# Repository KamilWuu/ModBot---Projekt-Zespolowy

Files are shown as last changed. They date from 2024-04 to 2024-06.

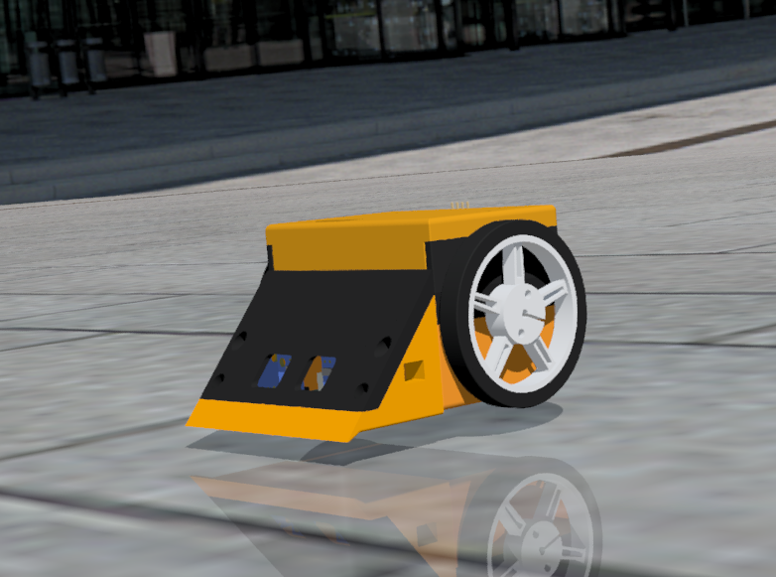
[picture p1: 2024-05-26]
images/render_!.png

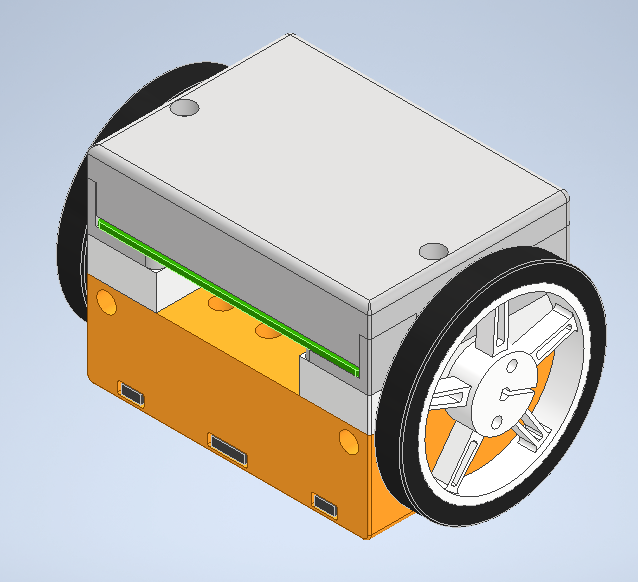
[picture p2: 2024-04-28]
images/main_module.png

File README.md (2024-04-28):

# ModBot---Projekt-Zespolowy


1 - Założenia projektowe
Robot modułowy ModBot będzie złożony z jednostki głównej – Platformy Mobilnej wraz z pilotem zdalnego sterowania za pomocą technologii Bluetooth. Platforma ta będzie miała możliwość
doczepienia modułów określających przeznaczenie robota:

• moduł MiniSumo,

• moduł LineFollower,

• Chwytak

2 - Cel i zakres projektu
Celem projektu jest stworzenie uniwersalnej platformy robotycznej pozwalającej na edukację
w zakresie elektroniki i programowania. Osobie uczącej się przy pomocy robota będzie da-
na możliwość samodzielnego złożenia oraz zamontowania wcześniej przygotowanych modułów,
dzięki którym robot będzie mógł wykonywać określone zadanie. Planowane są trzy domyślne
konfiguracje, za pomocą których robot będzie mógł wykonać następujące zadania:

• LineFollower – podążanie wzdłuż czarnej linii kontrastowej na białym tle, która nie posiada
zakrętów ostrzejszych niż 90◦.

• RoboSumo – przesunięcie kostki o masie zbliżonej do masy robota z standardowego ringu
Minisumo i pozostanie na ringu. Ma to na celu symulacje walki z zawodów robotycznych
z kategorii MiniSumo.

• Chwytak – utrzymanie obiektu o znacznie mniejszej masie niż jego własne poprzez moduł
zdalnego sterowania.

3 - Skład zespołu:
Kamil Winnicki - Mechanika i embedded,

Oliwier Woźniak -  Elektronika,

Patryk Peroński - Oprogramowanie i embeeded,

Rafał Koziołek - Mechanika i elektronika,

Jakub Frąckowiak - Kierownik zespołu, organizacja pracy,

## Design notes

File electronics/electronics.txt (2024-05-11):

Zanim zaczniecie cokolwiek robić, prosiłbym o posprzątanie warsztatu mechanicznego. Nawet jeśli NIE BĘDZIE "wielkiego sprzątania piwnicy". Przy czym nie mówie tu odrazu że macie zrobić wszystko na błysk.  Obecnie narzędzia rozwalone są po całej piwnicy i randomowych case'ach a piwnica jest cała w wiórach. 
PS. Gajowy nie jest od tego żeby po wszystkich sprzątać, a smieci można wyrzucić bez jego ingerencji.

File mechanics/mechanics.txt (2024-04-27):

backend i frontend - java script

Framework - react mui

czysty mysql

HOTEL:
- piętra, numer pokoju - numer pokoju zaczyna się od piętra

Pokoj
- numer pokoju
- pietro
- liczba lozek
- liczba miejsca
- standard pokoju
- cena za osobe
- cena za pokoj
- kuchnia czy jest

Rezerwacja:
mozna wyszukac po wlasnosciach pokoju, po liczbie miejsc
wpisywac ludzi co drugi pokoj
- data

aplikacja webowa

sortowanie
filtr
cena itp

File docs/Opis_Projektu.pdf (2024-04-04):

## Politechnika Wrocławska

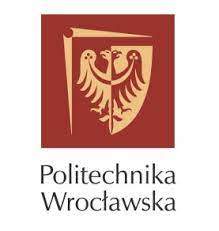
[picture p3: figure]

### Projekt Zespołowy Robot Modułowy ModBot

### Wydział: W12N Prowadzący: Dr inż. Robert Muszyński

Autorzy:

Kamil Winnicki
Oliwier Woźniak
Patryk Peroński
Rafał Koziołek
Jakub Frąckowiak
Wrocław, Polska | 4 kwietnia 2024

### Spis treści

1 Założenia projektowe | 1
2 Plan pracy i rozkład w czasie | 2
3 Doręczenie | 3
4 Budżet | 3
5 Zarządzanie projektem | 4
6 Skład zespołu | 4

### 1 Założenia projektowe

Robot modułowy ModBot będzie złożony z jednostki głównej – Platformy Mobilnej wraz z pilotem zdalnego sterowania za pomocą technologii Bluetooth. Platforma ta będzie miała możliwość doczepienia modułów określających przeznaczenie robota:
- moduł MiniSumo,
- moduł LineFollower,
- Chwytak.

### 1.1 Cel i zakres projektu

Celem projektu jest stworzenie uniwersalnej platformy robotycznej pozwalającej na edukację w zakresie elektroniki i programowania. Osobie uczącej się przy pomocy robota będzie dana możliwość samodzielnego złożenia oraz zamontowania wcześniej przygotowanych modułów, dzięki którym robot będzie mógł wykonywać określone zadanie. Planowane są trzy domyślne konfiguracje, za pomocą których robot będzie mógł wykonać następujące zadania:
- LineFollower – podążanie wzdłuż czarnej linii kontrastowej na białym tle, która nie posiada zakrętów ostrzejszych niż 90◦
- RoboSumo – przesunięcie kostki o masie zbliżonej do masy robota z standardowego ringu Minisumo i pozostanie na ringu. Ma to na celu symulacje walki z zawodów robotycznych z kategorii MiniSumo.
- Chwytak – utrzymanie obiektu o znacznie mniejszej masie niż jego własne poprzez moduł zdalnego sterowania.

### 1.2 Mechanika

W celu wzbudzenia większego zainteresowania wśród potencjalnych odbiorców, konstrukcja będzie składać się z wcześniej przygotowanych przez nas ”bloków”, w pewnym stopniu pozwalających na dostosowanie wyglądu takiego robota. Wykonane one bedą głównie z materiałów używanych powszechnie w druku 3D takich jak PLA lub PET-G.
W układzie napędowym robota zostaną zastosowane dwa silniki szczotkowe typu Pololu N20, które będą sterowane za pomocą układu różnicowego. W module chwytaka zostanie zastosowany serwomechanizm o wadze dziewięciu gramów.

### 1.3 Elektronika

Elektronika jako główną jednostkę obliczeniową będzie używać mikrokontrolera ESP32 - S3, ze względu na wbudowaną antenę WiFi/Bluetooth oraz prostotę implementacji.
Do sterowania silnikami zostanie zastosowany sterownik TB6612FNG, zawierający m.in podwójny mostek H.
W module MiniSumo użyte zostaną czujniki laserowe VL53L0X oraz dwa czujniki odbiciowe KTIR0711S. Zostaną one także użyte w module LineFollower w ilości 12 sztuk.

### 1.4 Oprogramowanie

Projekt zakłada programowanie Platformy Mobilnej za pomocą prostego środowiska graficznego korzystającego z bloków funkcyjnych. Program zostanie napisany w języku Scratch ze względu na popularność w sektorze edukacyjnym, prostotę obsługi oraz wsparcie dla dodatkowych rozszerzeń.
Program będzie kompatybilny ze środowiskiem Arduino, zapewniający podstawowe bloki funkcyjne m.in do odczytu czy ustawiania pinów, odczytów wejść analogowych, sterowaniu wyjściami PWM oraz obsłudze bibliotek pod popularne urządzenia peryferyjne takie jak: czujniki odległości TOF VL53L0X, serwomechanizmów i czujników laserowych.
Środowisko zapewni gotowe bloczki do obsługi modułów robota, dzięki którym nawet osoby bez doświadczenia w programowaniu powinny być w stanie zaprogramować swojego robota.

### 2 Plan pracy i rozkład w czasie

Ze względu na modułowość projektu, logicznym jest podział projektu na segmenty spełniających konkretne funkcje. W związku z tym nasz projekt podzieliliśmy na następujące zadania:
1. ustalenie interfejsów łączących poszczególne moduły,
2. zaprojektowanie i stworzenie głównego modułu sterującego,
3. napisanie i wdrożenie środowiska do programowania blokowego,
4. zaprojektowanie i stworzenie modułu napędowego,
5. zaprojektowanie i stworzenie modułu LineFollowera,
6. zaprojektowanie i stworzenie modułu MiniSumo,
7. zaprojektowanie i stworzenie modułu chwytaka oraz pilota służącego do zdalnego sterowania.

### 2.1 Kamienie milowe

Jak widać wszystkie te punkty (z wyjątkiem punktu pierwszego) podzielone są na dwa etapy, dzielące się na planowanie i realizację. Wszystkie te zadania, a w szczególności trzy ostatnie, mogą być wykonywane równolegle. Jednak preferowany jest tryb wykonywania zadań zgodny z powyższą numeracją. Zadania złożyliśmy na konkretne kamienie milowe.
Cechą tego rozwiązania jest złożoność zadań – składają się one z dwóch etapów: planowania i realizacji. Ponadto modułowość projektu sprawia, że punkty mogą być wykonywane równolegle i niezależnie od siebie. Jednak preferowany jest tryb wykonywania zadań zgodny z powyższą numeracją. Zadania zostały rozłożone na konkretne kamienie milowe.

### 2.1.1 Zakończenie fazy projektowej

Etap polega na stworzeniu schematów oraz przetestowaniu konkretnych elementów modułów. Po zakończeniu tego etapu będzie można zamówić wszystkie elementy elektroniczne oraz płytki PCB.

### 2.1.2 Synteza fizycznej części projektu

Po otrzymaniu płytek PCB oraz elementów elektronicznych zostaną rozpoczęte testy pojedynczych modułów. Działające płytki zostaną połączone i przetestowane za pomocą prostych programów. Kamień milowy zostanie osiągnięty, w momencie kiedy sygnały wysyłane z modułu głównego układu spotkają się z pożądaną reakcją modułu sterowanego (na przykład silniki będą się kręciły w odpowiednią stronę i zadaną prędkością).

### 2.1.3 Połączenie części fizycznej oraz programowej

Efektem tego etapu będzie gotowy produkt. Poprawne działanie robota po tym etapie oznaczać będzie osiągnięcie celu.

### 3 Doręczenie

Praca będzie jawna, dokumenty i efekty końcowe będą publikowane na platformie GitHub. Doręczenie projektu będzie odpowiadało etapom produkcji, zwieńczonymi realizacją kamieni milowych. Gdy kamień milowy zostanie osiągnięty, będzie wysłany dokument potwierdzający realizacje, zawierający następujące punkty:
- wskazanie co było kamieniem milowym,
- sposób realizacji,
- program oraz zdjęcia modułu robota,
- problemy oraz sposoby ich rozwiązania.
Do dokumentu będą sukcesywnie dodawane kolejne fragmenty o kamieniach milowych. Aktualizowany na bieżąco dokument zostanie przesyłany regularnie w terminach podanych poniżej.
Kamienie milowe | Termin realizacji | Zawartość podsumowania | Wskaźnik realizacji zadania
Zakończenie fazy projektowej | 30 kwietnia 2024 | Blokowe i ideowe schematy elektroniczne Modele części mechanicznych | Producent płytek PCB potwierdzi, że wszystkie płytki wchodzące w skład robota zostaną dopuszczone do produkcji
Synteza fizycznej części projektu | 7 czerwiec 2024 | Nagrania z działającymi modułami. Działanie będzie sygnalizonwane LED-ami oraz parametrami wyświetlanymi na ekranie OLED | Moduł sterujący poprawnie komunikuje się z modułami zadaniowymi, a robot jest w stanie się poruszać
Połączenie części fizycznej oraz programowej | 25 czerwiec 2024 | Nagrania i zdjęcia odpowiednich modułów robota, wykonujących zadania określone w głównym celu projektu | Modbot nie wyjedzie z określonej przestrzeni i wykryje przeciwnika. Modbot będzie poruszał się wzdłuż określonej trasy Modbot chwytakiem wykryje i chwyci klocek

### 4 Budżet

Nazwa | Opis | Szacowana ilość | Szacowany koszt [zł]
DC Pololu | Silniki DC | 2 | 100
ESP-32-S3 | mikrokontroler | 1 | 20
VL53L0X | czujnik laserowy odległości TOF | 2 | 40
VCNT2020 | czujnik odbiciowy | 15 | 50
Płytka PCB | FR4 dwuwarstwowa | 4 | 40
Filamet | 1kg PLA | 1 | 60
Zestaw elementów pasywnych | Elementy RLC w Formacie 0805 | 1 | 60
TB6612 | Sterownik silników DC dwukanałowy | 1 | 20
Servo SG90 | Serwomechanizm | 1 | 20
SSD1306 | Ekran OLED I2C 0.96 | 1 | 25
| | SUMA | 435

### 5 Zarządzanie projektem

### 5.1 Metodyka pracy

Do prowadzenia prac projektowych zostanie wykorzystana metodyka SCRUM. Pozwoli to na dynamiczne alokowanie zasobów ludzkich do rozwiązywania części krytycznych projektu. Pieczę nad realizacją celów będzie sprawował koordynator. Cele zostaną podzielone na tygodniowe sprinty, żeby pozwolić zarówno na dynamiczną pracę, jak i niskie obciążenie związane z planowaniem.

### 5.2 Środowisko zarządzania

Do zarządzania projektem zostało wybrane środowisko Trello. Wybór został dokonany ze względu na przejrzystość, łatwość i intuicyjność obsługi tego środowiska. Ponadto ważne dokumenty oraz części głównego dokumentu będą tam zawarte. Środowisko służyć będzie jako wspólne środowisko ułatwiające dzielenie się i przekazywanie plików projektowych, takich jak schematy i modele 3D. Dodatkowo, zostanie utworzone konto projektu na platformie GitLab, które będzie służyło upublicznieniu projektu oraz ułatwienie magazynowania programu sterującego robota modułowego.

### 5.3 Organizacja

Koordynator projektu będzie miał wgląd do pracy pozostałych członków projektu. Komunikacja odbywać się będzie na konwersacji na komunikatorze Messenger.

### 5.4 Rozwiązywanie konfliktów

Konflikty będą rozwiązywane na drodze mediacji celem wypracowania konsensusu dotyczącego spornej sprawy. Aby ułatwić negocjacje w trakcie trwania konfliktu. Rozmowa będzie głównym narzędziem radzenia sobie z konfliktami. Prowadzenie i rozstrzyganie mediacji będzie leżało w zakresie obowiązków koordynatora projektu.

### 6 Skład zespołu

### 6.1 Jakub Frąckowiak

Zakres obowiązków: Kierownik zespołu, organizacja pracy Umiejętności:
- tworzenia efektywnych arkuszy Excel,
- projektowanie 3D.
Doświadczenie:
- zarządzanie zakupami,
- lutowanie układów elektronicznych.

### 6.2 Kamil Winnicki

Zakres obowiązków: Mechanika i embedded Umiejętności:
- projektowanie oraz zrobienie wydruków 3D,

- programowanie mikrokontrolerów w języku C.
Doświadczenie:
- zaprojektowanie 4 osiowego manipulatora oraz robota minisumo
- prowadzenie warsztaów z mechaniki

### 6.3 Oliwier Woźniak

Zakres obowiązków: Elektronika
Umiejętności:
- czytanie dokumentacji,
- obsługa narzędzędzi do projektowania układów elektronicznych, takich jak KiCad, oraz Eagle,
- obsługa przyrządów lutowniczych.
Doświadczenie:
- prowadzenie warsztatów z elektroniki,
- zaprojektowanie, oraz realizacja układu licznika.

### 6.4 Patryk Peroński

Zakres obowiązków: Oprogramowanie, embeeded Umiejętności:
- programowanie C++, Python, JS,
- projektowanie PCB i elektroniki. Doświadczenie:
- robot edukacyjno-społeczny KapiBara,
- własne projekty PCB,
- hobbistyczne programy napisane w wyżej wspomnianych językach.

### 6.5 Rafał Koziołek

Zakres obowiązków: Mechanika i elektronika
Umiejętności:
- obsługa narzędzi i maszyn,
- zbudowanie robota minisumo.
Doświadczenie:
- praca w zakładzie produkcyjnym,
- koordynacja zawodów robotycznych Robotic Arena XV.

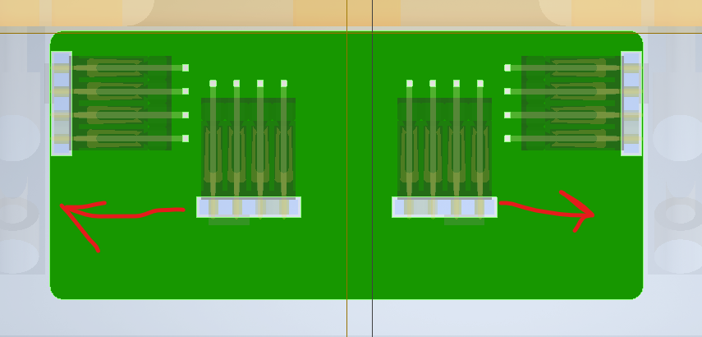
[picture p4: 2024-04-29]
images/MS_BOARD.png

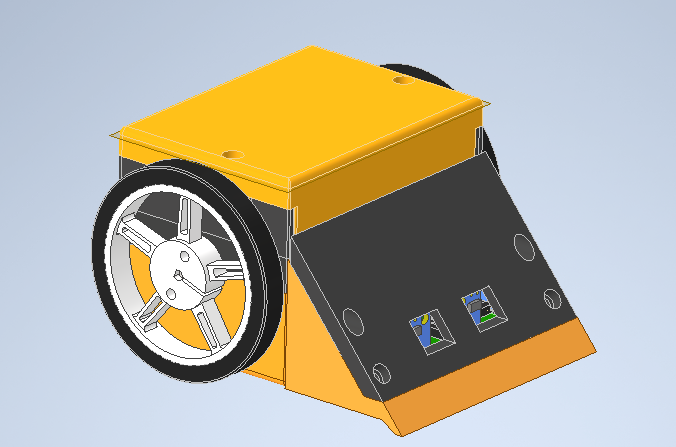
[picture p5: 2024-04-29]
images/Sumo_module.png

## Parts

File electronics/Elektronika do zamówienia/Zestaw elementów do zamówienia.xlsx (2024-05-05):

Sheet: Płytka główna
Reference | Value | Datasheet | Footprint | Qty | DNP
C1,C2 | 100nF | ~ | Capacitor_SMD:C_0402_1005Metric_Pad0.74x0.62mm_HandSolder | 2 | 1
C3,C8 | 0.1uF | ~ | Capacitor_SMD:C_0603_1608Metric | 2 | 1
C4,C5 | 22uF | ~ | Capacitor_SMD:C_0805_2012Metric | 2 | 1
C6,C7 | 10uF | ~ | Capacitor_SMD:C_0805_2012Metric | 2 | 1
C9,C10,C11,C12 | 10nF | ~ | Capacitor_SMD:C_0402_1005Metric_Pad0.74x0.62mm_HandSolder | 4 | 1
D1,D2,D3,D4,D5,D6,D7,D8 | LED | ~ | LED_SMD:LED_0402_1005Metric | 8 | 1
IC1 | TPS563201DDCR | http://www.ti.com/lit/gpn/tps563201 | User_defined_footprints:SOT95P280X110-6N | 1 | 1
J1 | ESP32_1 | ~ | Connector_PinSocket_2.54mm:PinSocket_1x14_P2.54mm_Vertical | 1 | 1
J2 | ESP32_2 | ~ | Connector_PinSocket_2.54mm:PinSocket_1x14_P2.54mm_Vertical | 1 | 1
J3 | M1_OUT | ~ | Connector_PinSocket_2.54mm:PinSocket_1x03_P2.54mm_Vertical | 1 | 1
J4 | M1_IN | ~ | Connector_PinSocket_2.54mm:PinSocket_1x03_P2.54mm_Vertical | 1 | 1
J5 | M2_IN | ~ | Connector_PinSocket_2.54mm:PinSocket_1x03_P2.54mm_Vertical | 1 | 1
J6 | M2_OUT | ~ | Connector_PinSocket_2.54mm:PinSocket_1x03_P2.54mm_Vertical | 1 | 1
J7 | I2C_OUT | ~ | Connector_JST:JST_EH_B4B-EH-A_1x04_P2.50mm_Vertical | 1 | 1
J8 | battery_connector | ~ | Connector_PinHeader_2.54mm:PinHeader_1x02_P2.54mm_Vertical | 1 | 1
J9 | V_Select | ~ | Connector_PinHeader_2.54mm:PinHeader_1x03_P2.54mm_Vertical | 1 | 1
J10 | BATT_SW | ~ | Connector_PinHeader_2.54mm:PinHeader_1x03_P2.54mm_Vertical | 1 | 1
J11 | OLED | ~ | Connector_PinSocket_2.54mm:PinSocket_1x04_P2.54mm_Vertical | 1 | 1
J12 | Złącze PCA | ~ | User_defined_footprints:ARK 01x02 5mm | 1 | 1
J14 | USB_B_Micro | https://www.tme.eu/pl/details/10118194-0001lf_c/zlacza-usb-i-ieee1394/amphenol-communications-solutions/10118194-0001lf/ | Connector_USB:USB_Micro-B_Amphenol_10118194_Horizontal | 1 | 1
L1 | 2.2uH | ~ | Inductor_SMD:L_Bourns_SRP7028A_7.3x6.6mm | 1 | 1
R1,R2,R10,R12,R20,R21,R23,R26 | 10kR | ~ | -- różne wartości -- | 8 | 1
R3,R4,R5,R6 | 2,4kR | ~ | Resistor_SMD:R_0402_1005Metric_Pad0.72x0.64mm_HandSolder | 4 | 1
R7,R8,R16,R22,R24,R25,R27 | 1kR | ~ | -- różne wartości -- | 7 | 1
R9 | 470R | ~ | Resistor_SMD:R_0402_1005Metric_Pad0.72x0.64mm_HandSolder | 1 | 1
R11 | 33.2kR | ~ | Resistor_SMD:R_0603_1608Metric | 1 | 1
R13,R14,R15,R17,R18,R19 | 330R | ~ | -- różne wartości -- | 6 | 1
SW1,SW2,SW3,SW4 | SW_Push | ~ | Button_Switch_THT:SW_PUSH_6mm_H5mm | 4 | 1
U1 | CH340N | https://aitendo3.sakura.ne.jp/aitendo_data/product_img/ic/inteface/CH340N/ch340n.pdf | Package_SO:SOP-8_3.9x4.9mm_P1.27mm | 1 | 1

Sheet: Moduł Sumo
Reference | Value | Datasheet | Footprint | Qty | DNP
C1 | 22uF | ~ | Capacitor_SMD:C_0402_1005Metric_Pad0.74x0.62mm_HandSolder | 1 | 1
C2,C4 | 100nF | ~ | Capacitor_SMD:C_0402_1005Metric_Pad0.74x0.62mm_HandSolder | 2 | 1
J1 | Input | ~ | Connector_JST:JST_EH_B4B-EH-A_1x04_P2.50mm_Vertical | 1
J2 | OUT 1 | ~ | Connector_PinHeader_2.54mm:PinHeader_1x04_P2.54mm_Vertical | 1 | ?
J3 | OUT 2 | ~ | Connector_PinHeader_2.54mm:PinHeader_1x04_P2.54mm_Vertical | 1 | ?
J4 | OUT 3 | ~ | Connector_PinHeader_2.54mm:PinHeader_1x04_P2.54mm_Vertical | 1 | ?
J5 | OUT 4 | ~ | Connector_PinHeader_2.54mm:PinHeader_1x04_P2.54mm_Vertical | 1 | ?
J6 | RST_M | ~ | Connector_PinSocket_2.54mm:PinSocket_1x02_P2.54mm_Vertical | 1
J7 | Sense_OUT | ~ | Connector_JST:JST_EH_B4B-EH-A_1x04_P2.50mm_Vertical | 1
R1,R2,R3,R4,R5,R6,R7,R8,R12,R13,R35 | 2,2kR | ~ | Resistor_SMD:R_0402_1005Metric_Pad0.72x0.64mm_HandSolder | 11 | 1
U1 | TCA9548APWR | http://www.ti.com/lit/ds/symlink/tca9548a.pdf | Package_SO:TSSOP-24_4.4x7.8mm_P0.65mm | 1 | 1

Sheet: Moduł LF x4
Reference | Value | Datasheet | Footprint | Qty | DNP
D1,D2,D3,D4 | LED | ~ | LED_SMD:LED_0402_1005Metric_Pad0.77x0.64mm_HandSolder | 4 | 1
J1 | Conn_01x06_Socket | ~ | Connector_JST:JST_XH_B6B-XH-AM_1x06_P2.50mm_Vertical | 1
R1,R6,R7,R12 | 330R | ~ | Resistor_SMD:R_0402_1005Metric_Pad0.72x0.64mm_HandSolder | 4 | 1
R2,R4,R8,R9 | 22kR | ~ | Resistor_SMD:R_0402_1005Metric_Pad0.72x0.64mm_HandSolder | 4 | 1
R3,R5,R10,R11 | 110R | ~ | Resistor_SMD:R_0402_1005Metric_Pad0.72x0.64mm_HandSolder | 4 | 1
RV1 | R_Potentiometer | ~ | User_defined_footprints:Potencjometr 3,2x3,4 | 1 | 1
U1 | LM2901 | https://www.st.com/resource/en/datasheet/lm2901.pdf | User_defined_footprints:SOIC127P600X175-14N | 1 | 1
U2,U3,U4,U5 | ITR8307-S17-TR8 | https://datasheet.lcsc.com/szlcsc/1810010232_Everlight-Elec-ITR8307-S17-TR8-B_C81632.pdf | OptoDevice:Everlight_ITR1201SR10AR | 4 | 1

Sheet: Hub LF
Reference | Value | Datasheet | Footprint | Qty | DNP
C1,C3 | 100nF | ~ | Capacitor_SMD:C_0402_1005Metric_Pad0.74x0.62mm_HandSolder | 2 | 1
C2 | 22uF | ~ | Capacitor_SMD:C_0402_1005Metric_Pad0.74x0.62mm_HandSolder | 1 | 1
D1,D2 | LED | ~ | LED_SMD:LED_0402_1005Metric_Pad0.77x0.64mm_HandSolder | 2 | 1
IC1 | MCP23018-E_SO | https://datasheet.datasheetarchive.com/originals/distributors/SFDatasheet-7/sf-000145813.pdf | User_defined_footprints:SOIC127P1030X265-28N | 1
J1 | OUT_1 | ~ | Connector_JST:JST_EH_B6B-EH-A_1x06_P2.50mm_Vertical | 1
J2 | IN | ~ | Connector_JST:JST_EH_B4B-EH-A_1x04_P2.50mm_Vertical | 1 | 1
J3 | OUT_2 | ~ | Connector_JST:JST_EH_B6B-EH-A_1x06_P2.50mm_Vertical | 1
J4 | OUT_3 | ~ | Connector_JST:JST_EH_B6B-EH-A_1x06_P2.50mm_Vertical | 1
J5 | OUT_4 | ~ | Connector_JST:JST_EH_B6B-EH-A_1x06_P2.50mm_Vertical | 1
J6 | RST_E | ~ | Connector_PinSocket_2.54mm:PinSocket_1x02_P2.54mm_Vertical | 1 | 1
R1 | 3kR | ~ | Resistor_SMD:R_0402_1005Metric_Pad0.72x0.64mm_HandSolder | 1 | 1
R2 | 13kR | ~ | Resistor_SMD:R_0402_1005Metric_Pad0.72x0.64mm_HandSolder | 1 | 1
R3 | 2,2kR | ~ | Resistor_SMD:R_0402_1005Metric_Pad0.72x0.64mm_HandSolder | 1 | 1
R4,R5 | 330R | ~ | Resistor_SMD:R_0402_1005Metric_Pad0.72x0.64mm_HandSolder | 2 | 1

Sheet: ESP32
Reference | Value | Datasheet | Footprint | Qty | DNP
C1,C4 | 100nF | ~ | Capacitor_SMD:C_0402_1005Metric_Pad0.74x0.62mm_HandSolder | 2 | 1
C2 | 22uF | ~ | Capacitor_SMD:C_0402_1005Metric_Pad0.74x0.62mm_HandSolder | 1 | 1
C3 | 1uF | ~ | Capacitor_SMD:C_0402_1005Metric_Pad0.74x0.62mm_HandSolder | 1 | 1
IC1 | ESP32-WROOM-32E-N4 | https://www.espressif.com/sites/default/files/documentation/esp32-wroom-32e_esp32-wroom-32ue_datasheet_en.pdf | User_defined_footprints:ESP32WROOM32EN4 | 1 | 1
J1,J2 | Conn_01x14_Pin | ~ | Connector_PinHeader_2.54mm:PinHeader_1x14_P2.54mm_Vertical | 2 | 1
J3 | UART | ~ | Connector_PinHeader_2.54mm:PinHeader_1x04_P2.54mm_Vertical | 1 | 1
R1,R2 | 10kR | ~ | Resistor_SMD:R_0402_1005Metric_Pad0.72x0.64mm_HandSolder | 2 | 1
SW1 | EN | ~ | Button_Switch_SMD:SW_Push_1P1T_XKB_TS-1187A | 1 | 1
SW2 | BOOT | ~ | Button_Switch_SMD:SW_Push_1P1T_XKB_TS-1187A | 1 | 1

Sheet: Sterowniki silników x2
Reference | Value | Datasheet | Footprint | Qty | DNP
C1 | 47uF | ~ | User_defined_footprints:CAPPM3528X210N | 1 | 1
D1,D2 | LED | ~ | Diode_SMD:D_0402_1005Metric_Pad0.77x0.64mm_HandSolder | 2 | 1
IC1 | DRV8210DRLR | https://www.ti.com/lit/ds/symlink/drv8210.pdf?ts=1641207817417 | User_defined_footprints:SOTFL50P160X60-6N | 1 | 1
J1,J2 | Conn_01x03_Pin | ~ | Connector_PinHeader_2.54mm:PinHeader_1x03_P2.54mm_Vertical | 2 | 1
R1,R2 | 1kR | ~ | Resistor_SMD:R_0402_1005Metric_Pad0.72x0.64mm_HandSolder | 2 | 1

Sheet: Podsumowanie
Nazwa elementu | Wartość | Wymagana ilość | Czy posiadamy | Link do zamówienia
Dioda | LED | 30 | Tak
Induktor | 2,2uH | 1 | Nie | https://www.lcsc.com/product-detail/Power-Inductors_BOURNS-SRP7028A-2R2M_C1329579.html
Kondensator ceramiczny | 22uF | 5 | Nie | https://www.lcsc.com/product-detail/Multilayer-Ceramic-Capacitors-MLCC-SMD-SMT_Murata-Electronics-GRM21BR61E226ME44L_C86816.html
Kondensator ceramiczny | 10uF | 2 | Nie | https://www.lcsc.com/product-detail/Multilayer-Ceramic-Capacitors-MLCC-SMD-SMT_FOJAN-FCC0805X106K250FT_C5137488.html
Kondensator ceramiczny | 1uF | 1 | Nie | https://www.lcsc.com/product-detail/Multilayer-Ceramic-Capacitors-MLCC-SMD-SMT_Samsung-Electro-Mechanics-CL05A105KP5NNNC_C14445.html
Kondensator ceramiczny | 100nF | 8 | Nie | https://www.lcsc.com/product-detail/Multilayer-Ceramic-Capacitors-MLCC-SMD-SMT_FH-Guangdong-Fenghua-Advanced-Tech-0603B104K500NT_C30926.html
Kondensator ceramiczny | 10nF | 4 | Nie | https://www.lcsc.com/product-detail/Multilayer-Ceramic-Capacitors-MLCC-SMD-SMT_YAGEO-CC0603KRX7R9BB103_C100042.html
Kondensator tantalowy | 47uF | 2 | Nie | https://www.lcsc.com/product-detail/Tantalum-Capacitors_CEC-Shenzhen-Zhenhua-XinYun-Elec-CA45-B-16V-47uF-K_C136751.html
Rezystor | 33,2kR | 1 | Nie
Rezystor | 22kR | 16 | Nie
Rezystor | 13kR | 1 | Nie
Rezystor | 10kR | 10 | Nie
Rezystor | 3kR | 1 | Nie
Rezystor | 2,4kR | 4 | Nie
Rezystor | 2,2kR | 12 | Nie
Rezystor | 1kR | 11 | Nie
Rezystor | 470R | 1 | Nie
Rezystor | 330R | 24 | Nie
Rezystor | 110R | 16 | Nie
Potencjometr | 10kR | 4 | Tak
Sterownik silnika | DRV8210DRLR | 2 | Tak
Mikrokontroler | ESP32-WROOM-32E-N4 | 1 | Tak
Ekspander portów | MCP23018-E_SO | 1 | Tak
Muttiplekser I2C | TCA9548APWR | 1 | Tak
Przetwornica step down | TPS563201DDCR | 1 | Nie | https://www.lcsc.com/product-detail/DC-DC-Converters_Texas-Instruments-TPS563201DDCR_C116592.html
Translator USB->UART | CH340N | 1 | Nie | https://www.lcsc.com/product-detail/USB-Converters_WCH-Jiangsu-Qin-Heng-CH340N_C2977777.html
Komparator | LM2901 | 4 | Tak
Czujnik odbiciowy | ITR8307-S17-TR8 | 16 | Tak
Goldpin | 01x02 męski | 1 | Nie
Goldpin | 01x02 żeński | 2 | Nie
Goldpin | 01x03 męski | 6 | Nie
Goldpin | 01x03 żeński | 4 | Nie
Goldpin | 01x04 męski | 1+4? | Nie
Goldpin | 01x14 męski | 2 | Nie
Goldpin | 01x14 żeński | 2 | Nie
JST | 01x04 męski | x | Tak
JST | 01x04 żeński | x | Tak
JST | 01x06 męski | 8 | Nie
JST | 01x06 żeński | 8 | Nie
Złącze ARK | 1x02 5mm | 1 | Nie
Złącze micro USB | Micro-B_Amphenol_10118194_Horizontal | 1 | Nie | https://www.lcsc.com/product-detail/USB-Connectors_span-style-background-color-ff0-Amphenol-span-ICC-10118194-0001LF_C132563.html
Przycisk ESP | - | 2 | Nie?
Przycisk Tact | - | 4 | Tak

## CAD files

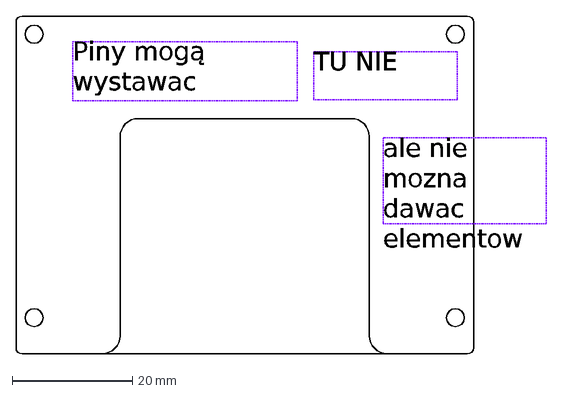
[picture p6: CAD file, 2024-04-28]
images/main_pcb_bottom-side_limits.dxf
TU NIE
Piny mogą wystawac
ale nie mozna dawac elementow

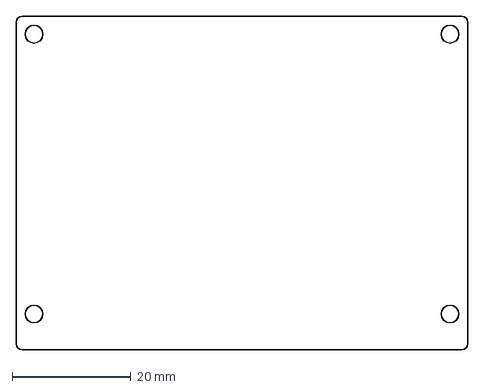
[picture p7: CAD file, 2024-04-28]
images/main_pcb_shape.dxf
76.0 x 56.1 mm

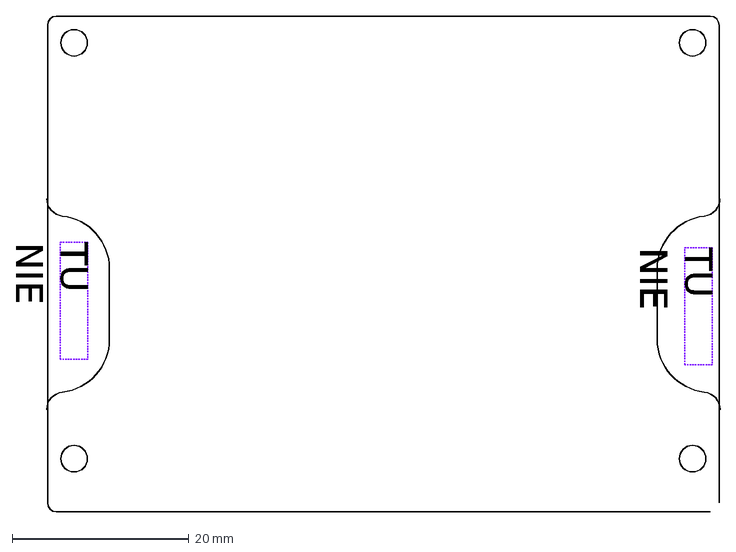
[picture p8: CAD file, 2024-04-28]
images/main_pcb_up-side_limits.dxf
TU NIE

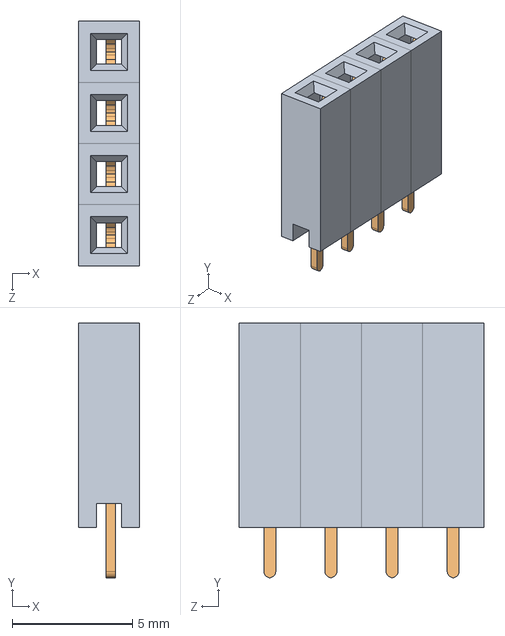
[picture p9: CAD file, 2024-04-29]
mechanics/STEP/Header_4.SLDASM
2.54 x 10.6 x 10.2 mm
header x 4
pin x 4

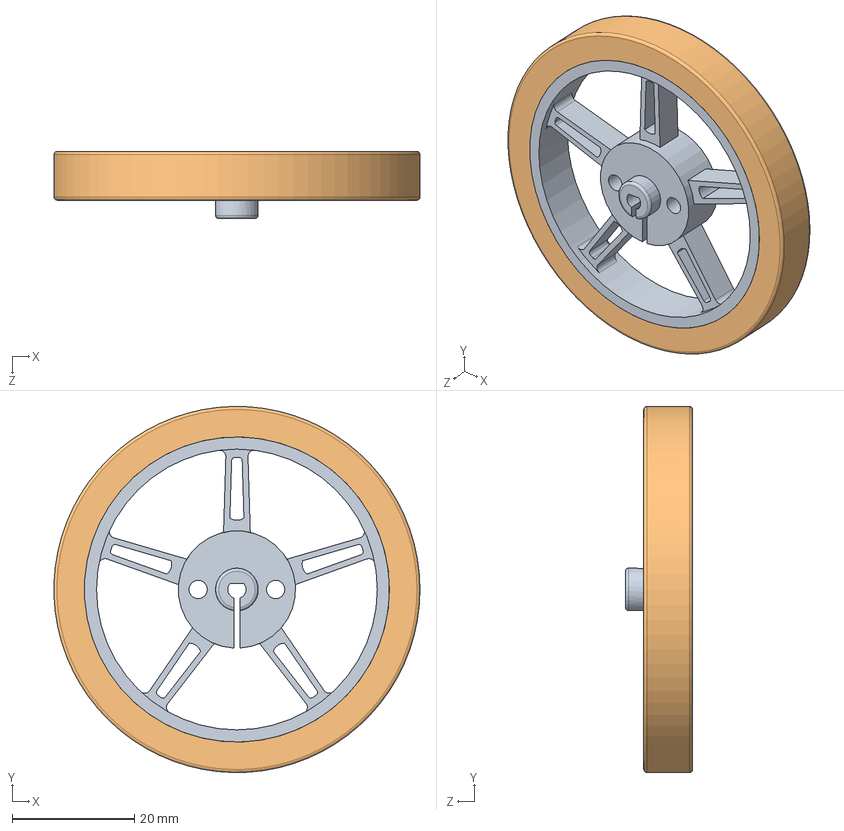
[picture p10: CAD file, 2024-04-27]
mechanics/STEP/PololuWheel 60x8mm.SLDASM
60.0 x 60.0 x 11.0 mm
Part2^PololuWheel 60x8mm
Part3^PololuWheel 60x8mm

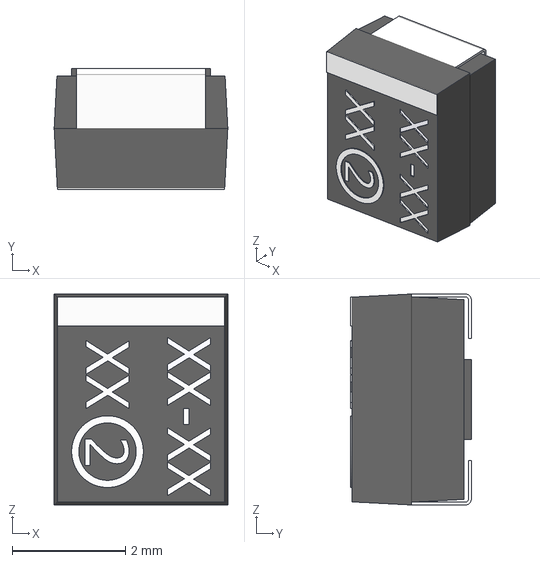
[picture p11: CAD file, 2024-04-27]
electronics/CAD Files/C_Tantal_B/3D/293D476X9010B2TE3.stp
3.07 x 2.13 x 3.73 mm

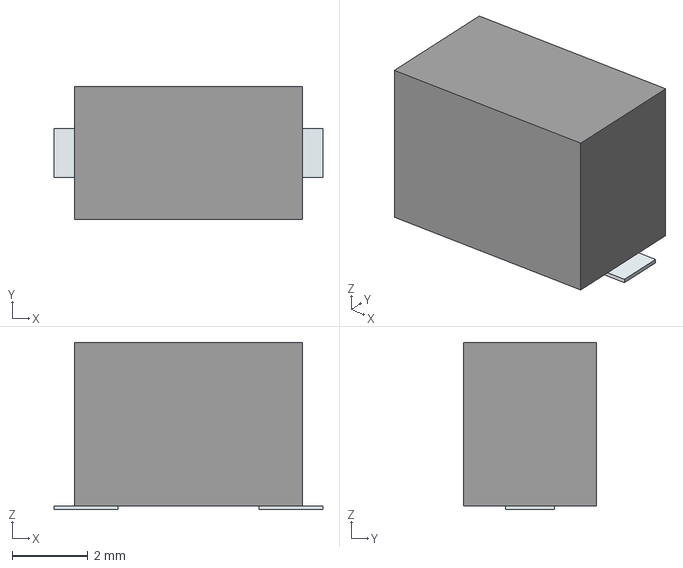
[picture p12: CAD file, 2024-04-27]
electronics/CAD Files/DIP_SW_2-PIN/3D/DTSM-31N-V-T_R.stp
7.08 x 3.50 x 4.40 mm
Pins

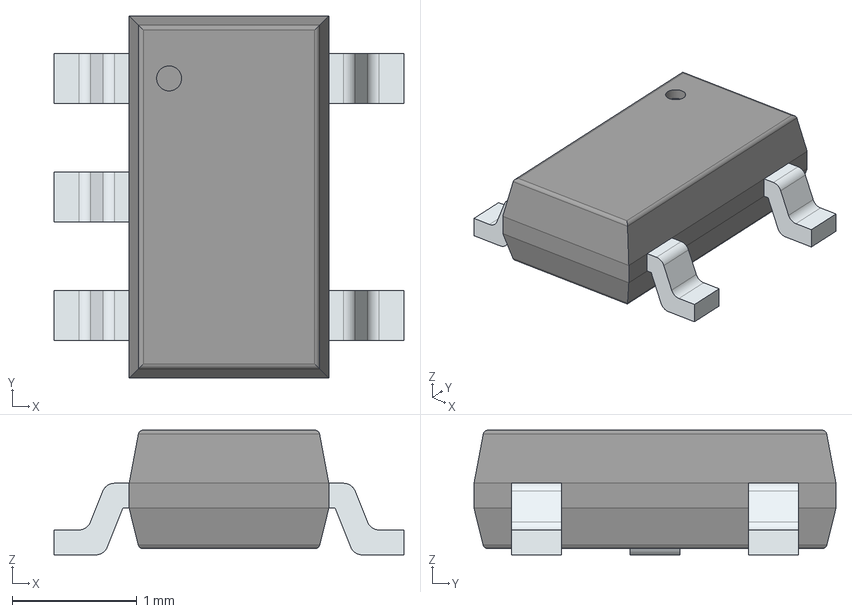
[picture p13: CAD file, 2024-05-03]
electronics/CAD Files/MIC2288YD5-TR/3D/MIC2288YD5-TR.stp
2.80 x 2.90 x 1.00 mm
PinsArrayL
PinsArrayR

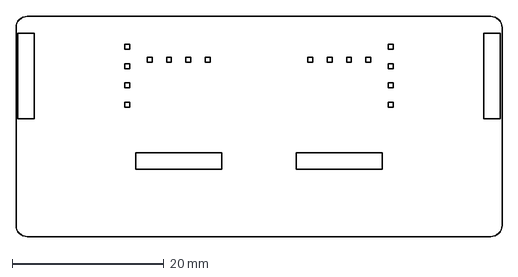
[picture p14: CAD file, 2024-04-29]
images/MS_board.dxf
64.0 x 29.0 mm

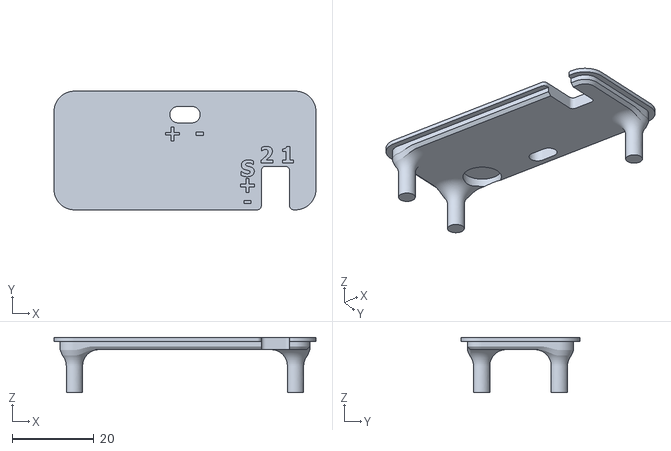
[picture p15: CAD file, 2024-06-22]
mechanics/druk/modul_chwytaka/pca_obudowa_gora.stl
64.0 x 29.0 x 13.5

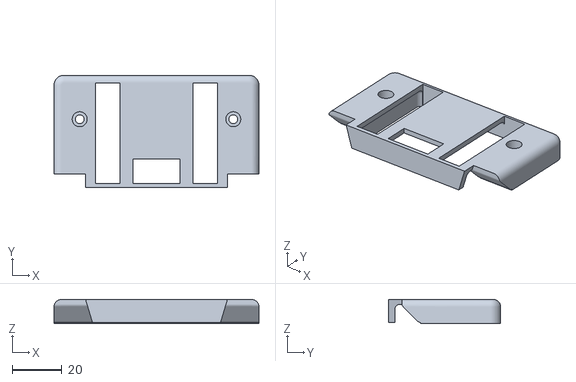
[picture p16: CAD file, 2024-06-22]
mechanics/druk/pokrywa.stl
82.0 x 45.0 x 9.65

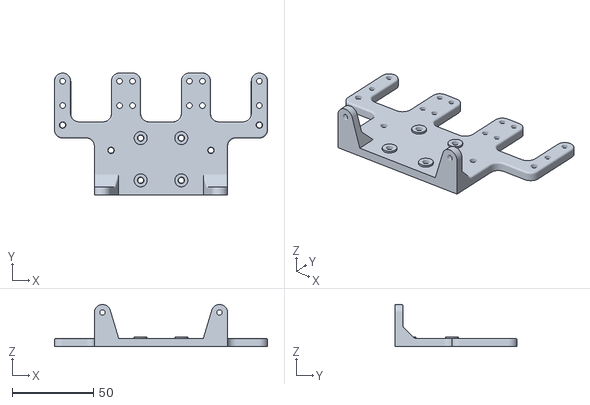
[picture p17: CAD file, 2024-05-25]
mechanics/lacznik.stl
131.0 x 75.0 x 25.9

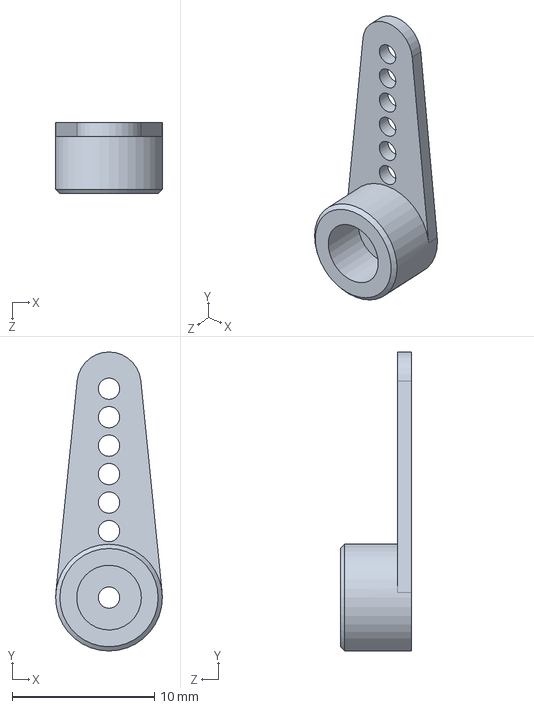
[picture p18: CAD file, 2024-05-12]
mechanics/modul_chwytaka/A1.SLDPRT
7.50 x 21.0 x 5.00 mm

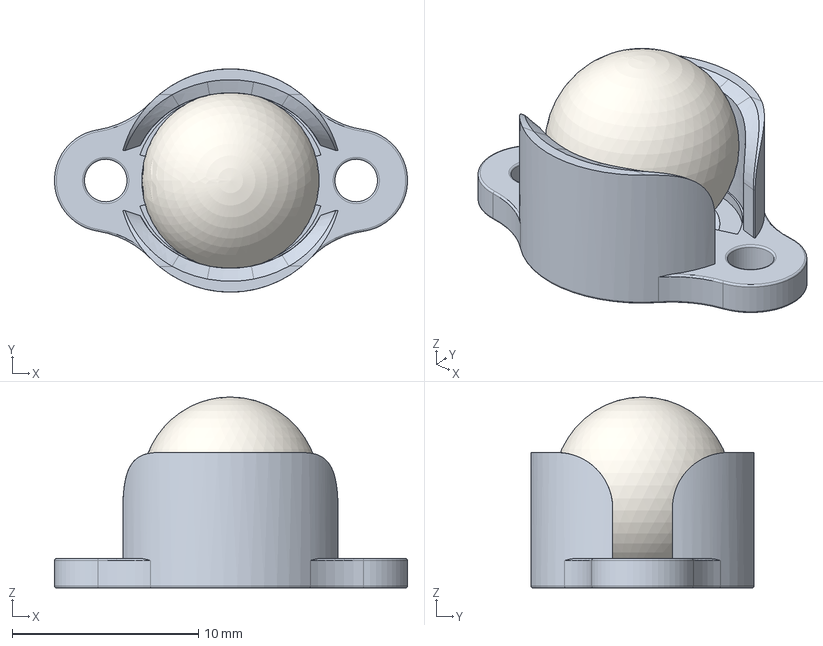
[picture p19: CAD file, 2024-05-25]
mechanics/STEP/Pololu Ball Caster with 3_8_ Metal Ball.stp
19.0 x 12.0 x 10.3 mm
Caster

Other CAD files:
mechanics/druk/modul_chwytaka/pca_obudowa_dol.stl
mechanics/druk/podpora_MIR.stl
mechanics/modul_chwytaka/Towerpro Micro Servo 9g.SLDPRT
mechanics/STEP/Moduł Sumo.step
electronics/CAD Files/C_Tantal_B/Allegro/cappm3528x210n.psm
electronics/CAD Files/C_Tantal_B/DEHDL/293d476x9010b2te3/chips/chips.prt
electronics/CAD Files/MCP23018-E_SO/3D/MCP23018-E_SO.stp
electronics/CAD Files/MCP73844-840I_MS/3D/MCP73844-840I_MS.stp
mechanics/1x4 Male Pin Header Angle.ipt
mechanics/1x4 Male Pin Header Angle_MIR.ipt
mechanics/2.iam
mechanics/LF.iam
mechanics/Li_Pol 800mAh.ipt
mechanics/MAIN.iam
mechanics/MS_PCB.ipt
mechanics/MS_Pokrywa.ipt
mechanics/MS_podstawa.ipt
mechanics/N20 DC MOTOR.ipt
mechanics/N20_Bracket_Extended_Pololu.ipt
mechanics/N20_Bracket_Extended_Pololu_MIR.ipt
mechanics/OldVersions/LF.0009.iam
mechanics/OldVersions/Li_Pol 800mAh.0002.ipt
mechanics/OldVersions/MAIN.0029.iam
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

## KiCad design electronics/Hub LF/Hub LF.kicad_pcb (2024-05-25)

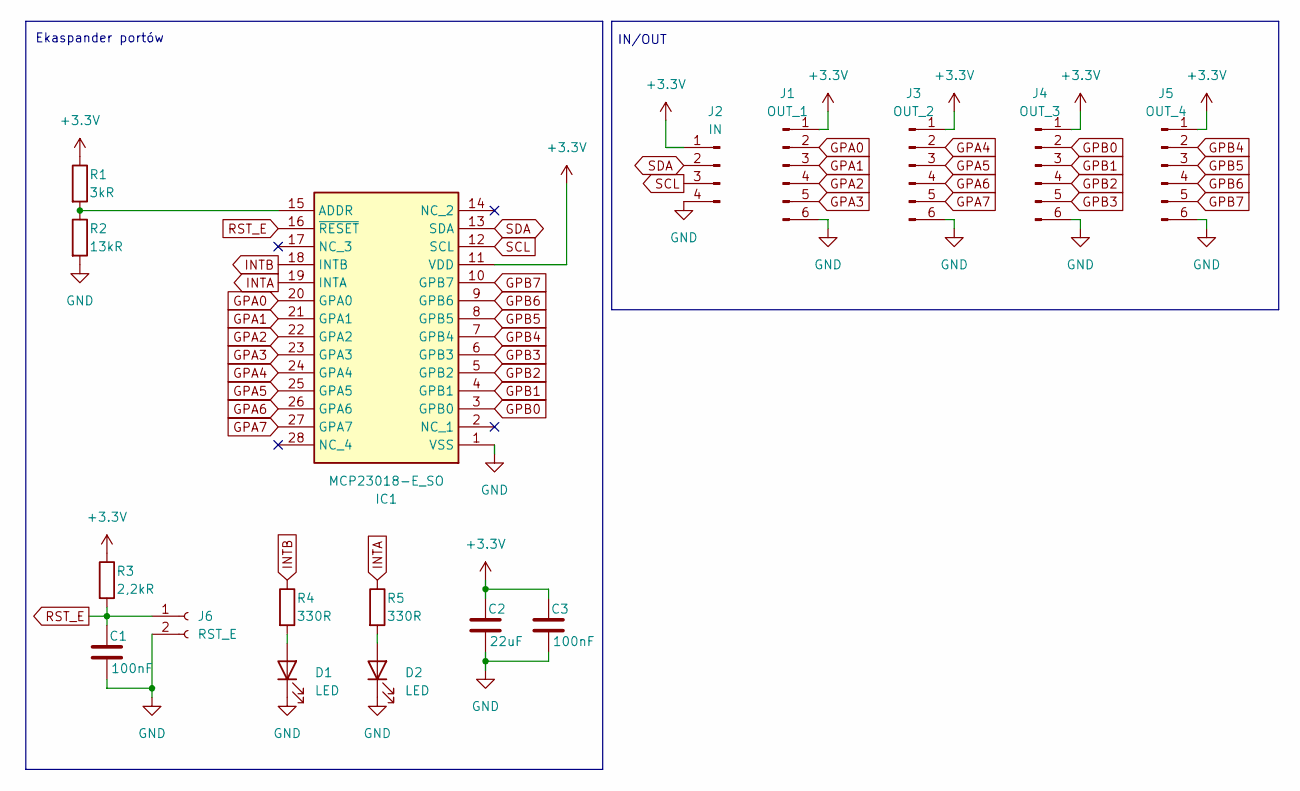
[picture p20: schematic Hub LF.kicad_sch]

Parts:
C1, C3: 100nF; C_0402_1005Metric_Pad0.74x0.62mm_HandSolder
C2: 22uF; C_0402_1005Metric_Pad0.74x0.62mm_HandSolder
D1, D2: LED; LED_0402_1005Metric_Pad0.77x0.64mm_HandSolder
IC1: MCP23018-E_SO; SOIC127P1030X265-28N; Manufacturer_Part_Number MCP23018-E/SO
J1: OUT_1; JST_EH_B6B-EH-A_1x06_P2.50mm_Vertical
J2: IN; JST_EH_B4B-EH-A_1x04_P2.50mm_Vertical
J3: OUT_2; JST_EH_B6B-EH-A_1x06_P2.50mm_Vertical
J4: OUT_3; JST_EH_B6B-EH-A_1x06_P2.50mm_Vertical
J5: OUT_4; JST_EH_B6B-EH-A_1x06_P2.50mm_Vertical
J6: RST_E; PinSocket_1x02_P2.54mm_Vertical
R1: 3kR; R_0402_1005Metric_Pad0.72x0.64mm_HandSolder
R2: 13kR; R_0402_1005Metric_Pad0.72x0.64mm_HandSolder
R3: 2,2kR; R_0402_1005Metric_Pad0.72x0.64mm_HandSolder
R4, R5: 330R; R_0402_1005Metric_Pad0.72x0.64mm_HandSolder

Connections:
+3.3V: C2.1, C3.1, IC1.11 (VDD), J1.1, J2.1, J3.1, J4.1, J5.1, R1.1, R3.1
GND: C1.2, C2.2, C3.2, D1.1 (K), D2.1 (K), IC1.1 (VSS), J1.6, J2.4, J3.6, J4.6, J5.6, J6.2, R2.2
GPA0: IC1.20 (GPA0), J1.2
GPA1: IC1.21 (GPA1), J1.3
GPA2: IC1.22 (GPA2), J1.4
GPA3: IC1.23 (GPA3), J1.5
GPA4: IC1.24 (GPA4), J3.2
GPA5: IC1.25 (GPA5), J3.3
GPA6: IC1.26 (GPA6), J3.4
GPA7: IC1.27 (GPA7), J3.5
GPB0: IC1.3 (GPB0), J4.2
GPB1: IC1.4 (GPB1), J4.3
GPB2: IC1.5 (GPB2), J4.4
GPB3: IC1.6 (GPB3), J4.5
GPB4: IC1.7 (GPB4), J5.2
GPB5: IC1.8 (GPB5), J5.3
GPB6: IC1.9 (GPB6), J5.4
GPB7: IC1.10 (GPB7), J5.5
INTA: IC1.19 (INTA), R5.1
INTB: IC1.18 (INTB), R4.1
unnamed: D1.2 (A), R4.2
unnamed: D2.2 (A), R5.2
unnamed: IC1.15 (ADDR), R1.2, R2.1
RST_E: C1.1, IC1.16 (~RESET), J6.1, R3.2
SCL: IC1.12 (SCL), J2.3
SDA: IC1.13 (SDA), J2.2

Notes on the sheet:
IN/OUT
Ekaspander portów

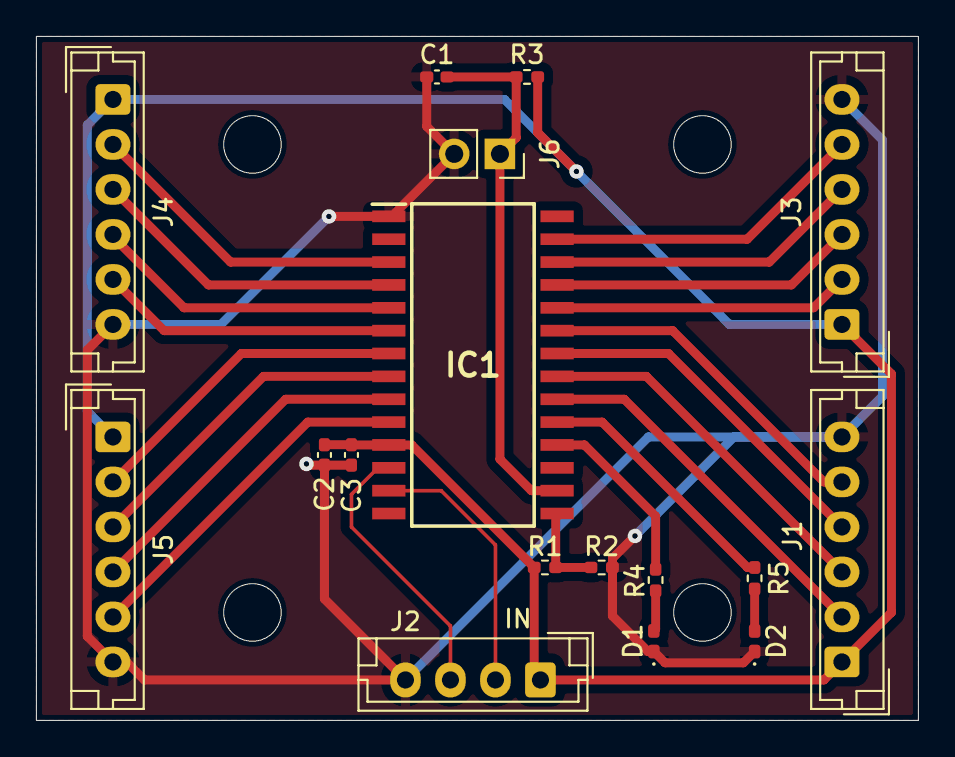
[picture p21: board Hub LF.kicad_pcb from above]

Board: 2 copper layers, 49.0 x 38.0 mm, 17 parts (0 on the bottom side), 26 nets.

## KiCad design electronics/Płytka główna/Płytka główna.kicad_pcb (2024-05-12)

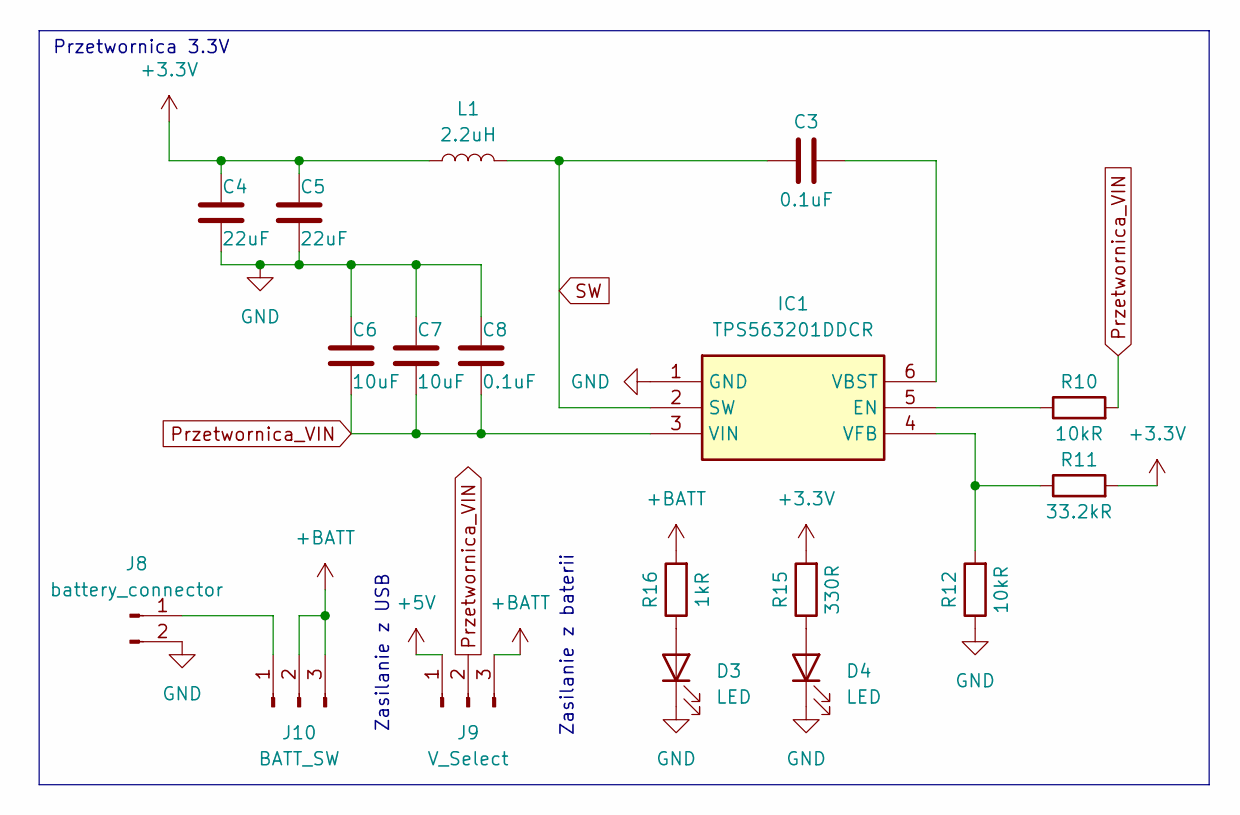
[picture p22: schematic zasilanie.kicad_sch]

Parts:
C3, C8: 0.1uF; C_0603_1608Metric
C4, C5: 22uF; C_0805_2012Metric
C6, C7: 10uF; C_0805_2012Metric
D3, D4: LED; LED_0402_1005Metric
IC1: TPS563201DDCR; SOT95P280X110-6N; Manufacturer_Part_Number TPS563201DDCR
J8: battery_connector; PinHeader_1x02_P2.54mm_Vertical
J9: V_Select; PinHeader_1x03_P2.54mm_Vertical
J10: BATT_SW; PinHeader_1x03_P2.54mm_Vertical
L1: 2.2uH; L_Bourns_SRP7028A_7.3x6.6mm
R10, R12: 10kR; R_0603_1608Metric
R11: 33.2kR; R_0603_1608Metric
R15: 330R; R_0603_1608Metric
R16: 1kR; R_0603_1608Metric

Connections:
+3.3V: C4.2, C5.2, L1.1, R11.2, R15.2; also elsewhere on the board
+5V: J9.1; also elsewhere on the board
+BATT: J9.3, J10.2, J10.3, R16.2; also elsewhere on the board
GND: C4.1, C5.1, C6.2, C7.2, C8.2, D3.1 (K), D4.1 (K), IC1.1 (GND), J8.2, R12.1; also elsewhere on the board
unnamed: D3.2 (A), R16.1
unnamed: D4.2 (A), R15.1
unnamed: IC1.5 (EN), R10.1
unnamed: C3.2, IC1.6 (VBST)
unnamed: IC1.4 (VFB), R11.1, R12.2
unnamed: J8.1, J10.1
Przetwornica_VIN: C6.1, C7.1, C8.1, IC1.3 (VIN), J9.2, R10.2
SW: C3.1, IC1.2 (SW), L1.2

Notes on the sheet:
Zasilanie z baterii
Przetwornica 3.3V
Zasilanie z USB

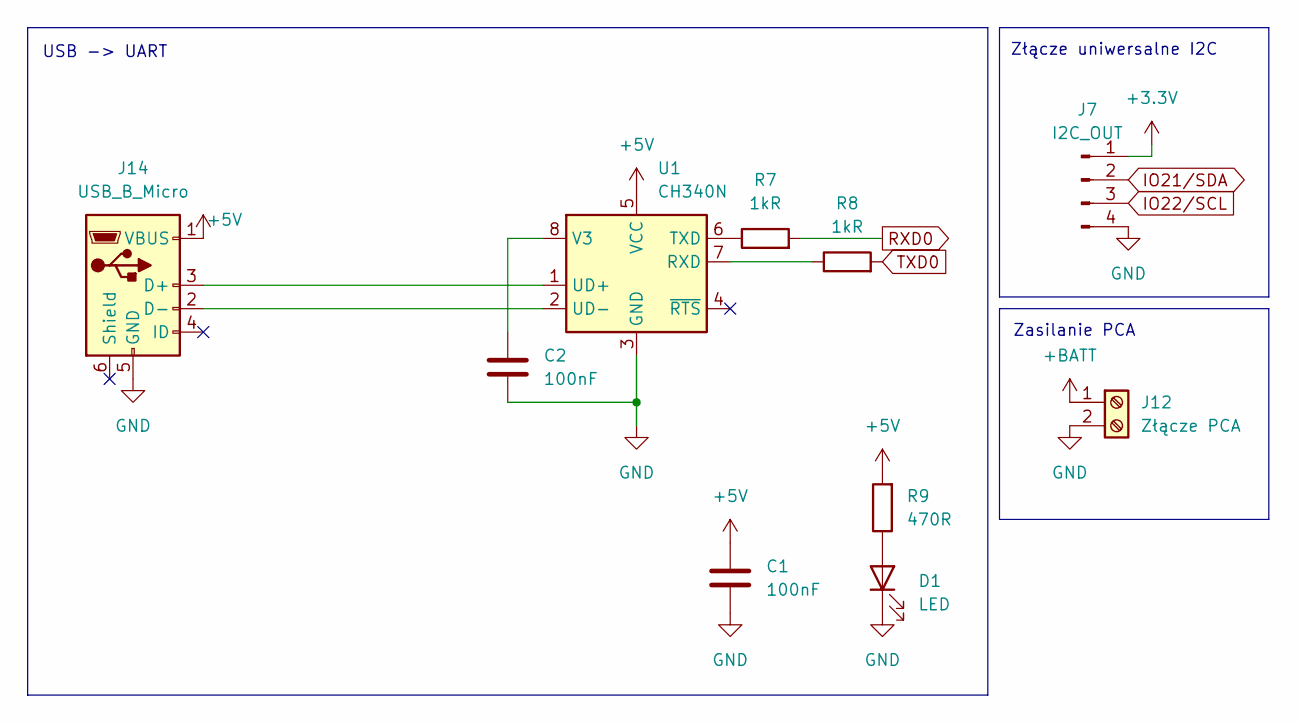
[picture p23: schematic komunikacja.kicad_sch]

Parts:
C1, C2: 100nF; C_0402_1005Metric_Pad0.74x0.62mm_HandSolder
D1: LED; LED_0402_1005Metric
J7: I2C_OUT; JST_EH_B4B-EH-A_1x04_P2.50mm_Vertical
J12: Złącze PCA; ARK 01x02 5mm
J14: USB_B_Micro; USB_Micro-B_Amphenol_10118194_Horizontal
R7, R8: 1kR; R_0402_1005Metric_Pad0.72x0.64mm_HandSolder
R9: 470R; R_0402_1005Metric_Pad0.72x0.64mm_HandSolder
U1: CH340N; SOP-8_3.9x4.9mm_P1.27mm

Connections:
+3.3V: J7.1; also elsewhere on the board
+5V: C1.1, J14.1 (VBUS), R9.2, U1.5 (VCC); also elsewhere on the board
+BATT: J12.1; also elsewhere on the board
GND: C1.2, C2.2, D1.1 (K), J7.4, J12.2, J14.5 (GND), U1.3 (GND); also elsewhere on the board
IO21/SDA: J7.2; also elsewhere on the board
IO22/SCL: J7.3; also elsewhere on the board
unnamed: D1.2 (A), R9.1
unnamed: J14.3 (D+), U1.1 (UD+)
unnamed: J14.2 (D-), U1.2 (UD-)
unnamed: R8.1, U1.7 (RXD)
unnamed: R7.1, U1.6 (TXD)
unnamed: C2.1, U1.8 (V3)
RXD0: R7.2; also elsewhere on the board
TXD0: R8.2; also elsewhere on the board

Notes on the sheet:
Zasilanie PCA
USB -> UART
Złącze uniwersalne I2C

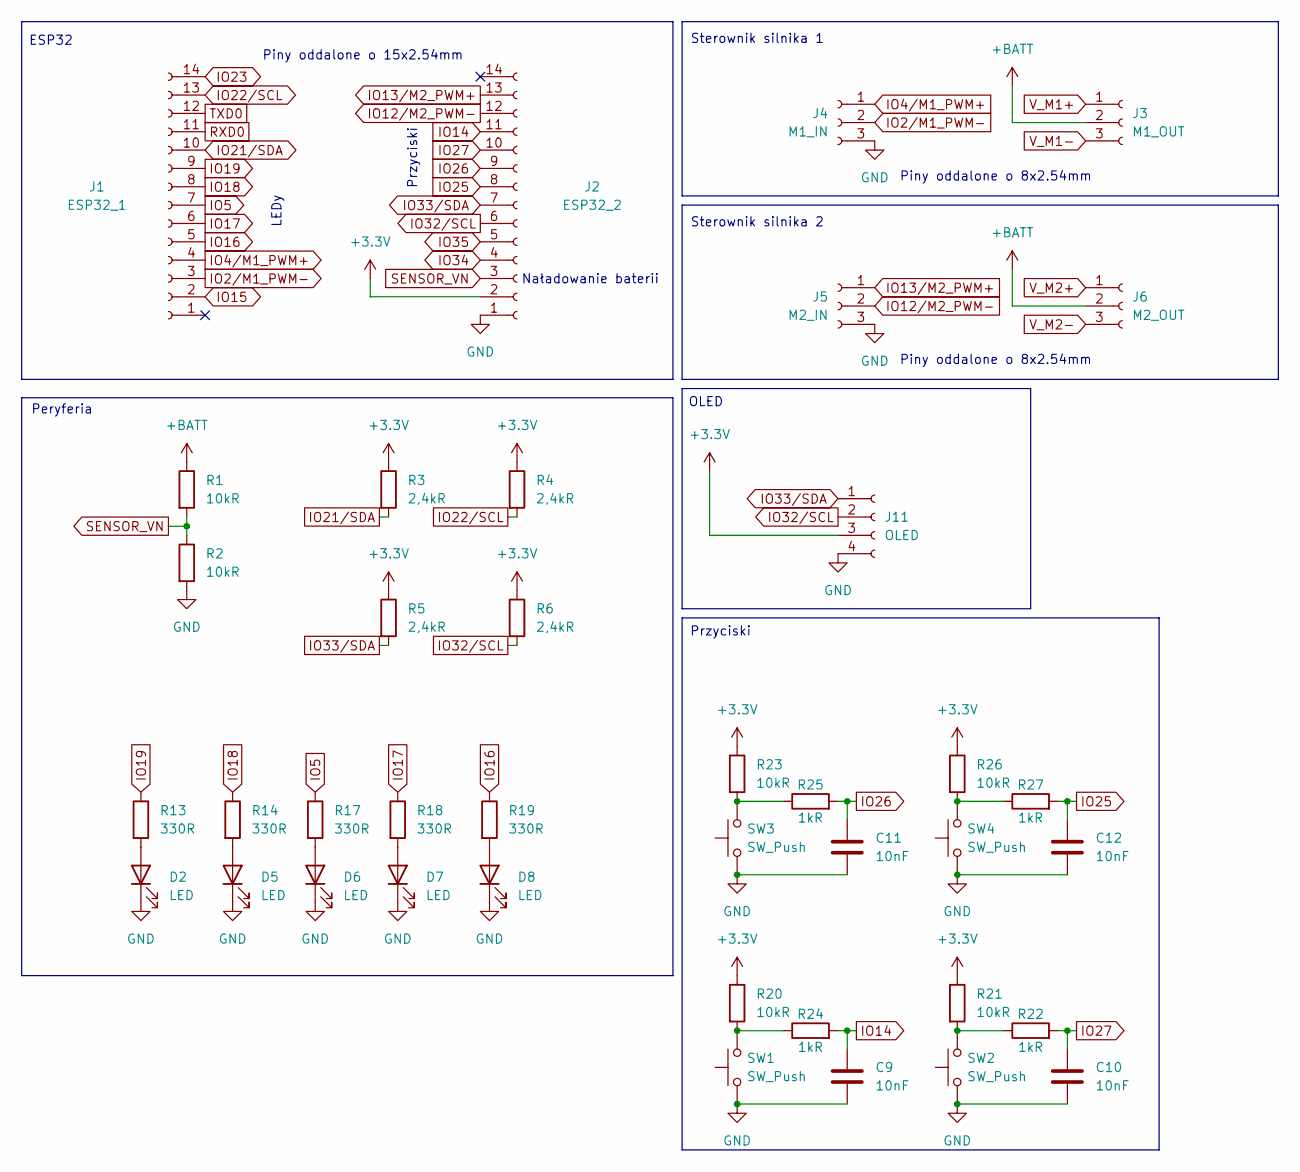
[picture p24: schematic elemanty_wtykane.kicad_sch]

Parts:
C9, C10, C11, C12: 10nF; C_0402_1005Metric_Pad0.74x0.62mm_HandSolder
D2, D5, D6, D7, D8: LED; LED_0402_1005Metric
J1: ESP32_1; PinSocket_1x14_P2.54mm_Vertical
J2: ESP32_2; PinSocket_1x14_P2.54mm_Vertical
J3: M1_OUT; PinSocket_1x03_P2.54mm_Vertical
J4: M1_IN; PinSocket_1x03_P2.54mm_Vertical
J5: M2_IN; PinSocket_1x03_P2.54mm_Vertical
J6: M2_OUT; PinSocket_1x03_P2.54mm_Vertical
J11: OLED; PinSocket_1x04_P2.54mm_Vertical
R1, R2, R20, R21, R23, R26: 10kR; R_0402_1005Metric_Pad0.72x0.64mm_HandSolder
R3, R4, R5, R6: 2,4kR; R_0402_1005Metric_Pad0.72x0.64mm_HandSolder
R13, R14, R17, R18, R19: 330R; R_0402_1005Metric_Pad0.72x0.64mm_HandSolder
R22, R24, R25, R27: 1kR; R_0402_1005Metric_Pad0.72x0.64mm_HandSolder
SW1, SW2, SW3, SW4: SW_Push; SW_PUSH_6mm_H5mm

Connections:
+3.3V: J2.2, J11.3, R3.1, R4.1, R5.1, R6.1, R20.1, R21.1, R23.1, R26.1; also elsewhere on the board
+BATT: J3.2, J6.2, R1.1; also elsewhere on the board
GND: C9.2, C10.2, C11.2, C12.2, D2.1 (K), D5.1 (K), D6.1 (K), D7.1 (K), D8.1 (K), J2.1, J4.3, J5.3, J11.4, R2.2, SW1.1, SW2.1, SW3.1, SW4.1; also elsewhere on the board
IO2/M1_PWM-: J1.3, J4.2
IO4/M1_PWM+: J1.4, J4.1
IO5: J1.7, R17.1
IO12/M2_PWM-: J2.12, J5.2
IO13/M2_PWM+: J2.13, J5.1
IO14: C9.1, J2.11, R24.2
IO15: J1.2
IO16: J1.5, R19.1
IO17: J1.6, R18.1
IO18: J1.8, R14.1
IO19: J1.9, R13.1
IO21/SDA: J1.10, R3.2; also elsewhere on the board
IO22/SCL: J1.13, R4.2; also elsewhere on the board
IO23: J1.14
IO25: C12.1, J2.8, R27.2
IO26: C11.1, J2.9, R25.2
IO27: C10.1, J2.10, R22.2
IO32/SCL: J2.6, J11.2, R6.2
IO33/SDA: J2.7, J11.1, R5.2
IO34: J2.4
IO35: J2.5
unnamed: D2.2 (A), R13.2
unnamed: D5.2 (A), R14.2
unnamed: D6.2 (A), R17.2
unnamed: D7.2 (A), R18.2
unnamed: D8.2 (A), R19.2
unnamed: R20.2, R24.1, SW1.2
unnamed: R21.2, R22.1, SW2.2
unnamed: R23.2, R25.1, SW3.2
unnamed: R26.2, R27.1, SW4.2
RXD0: J1.11; also elsewhere on the board
SENSOR_VN: J2.3, R1.2, R2.1
TXD0: J1.12; also elsewhere on the board
V_M1+: J3.1
V_M1-: J3.3
V_M2+: J6.1
V_M2-: J6.3

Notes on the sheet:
OLED
Peryferia
Przyciski
Piny oddalone o 8x2.54mm
Sterownik silnika 1
Naładowanie baterii
LEDy
ESP32
Sterownik silnika 2
Piny oddalone o 15x2.54mm
Przyciski

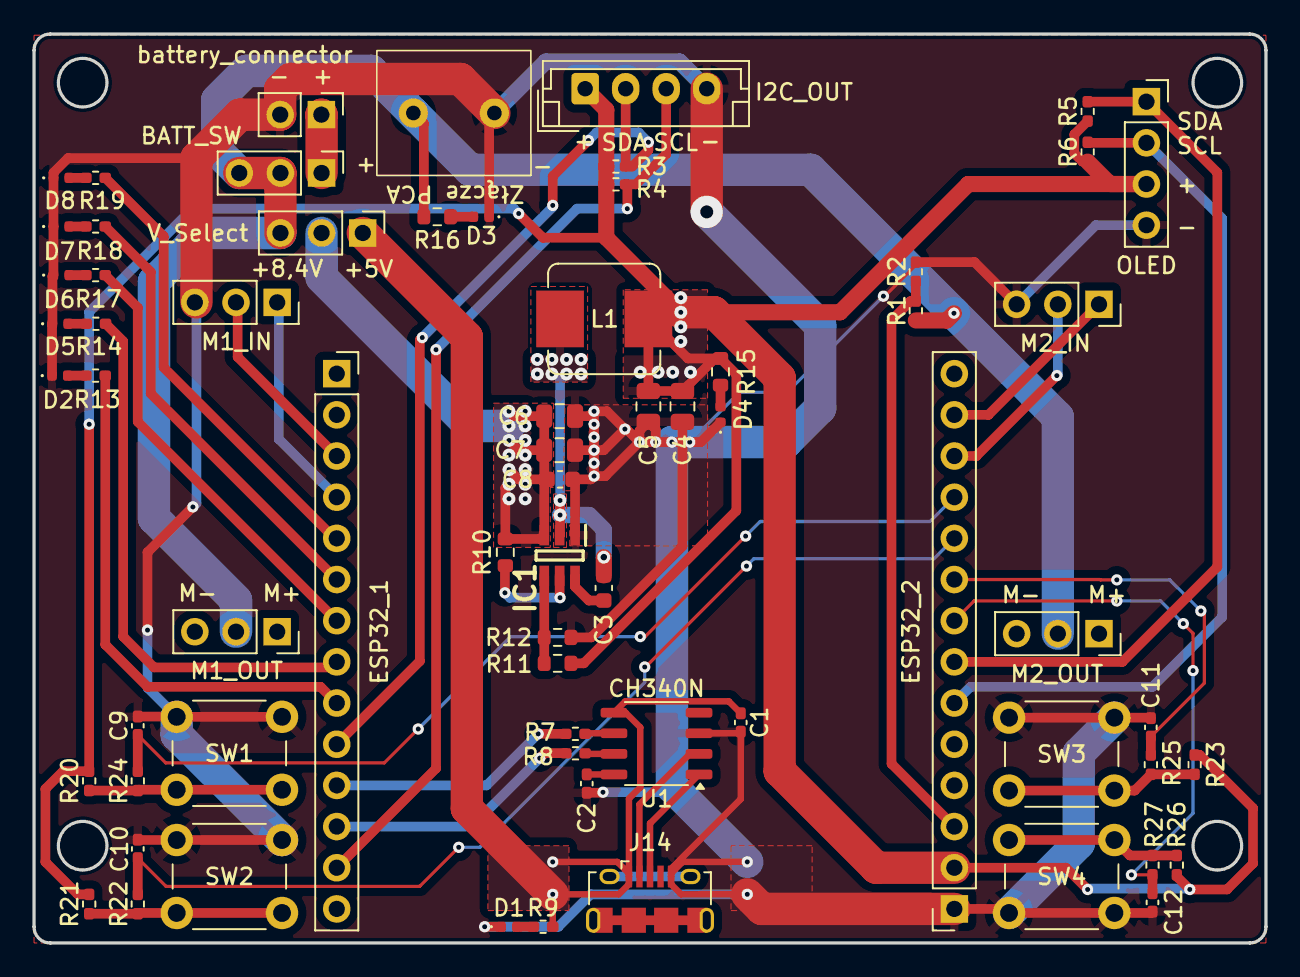
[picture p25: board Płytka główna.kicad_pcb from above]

Board: 2 copper layers, 76.0 x 56.1 mm, 67 parts (0 on the bottom side), 47 nets.

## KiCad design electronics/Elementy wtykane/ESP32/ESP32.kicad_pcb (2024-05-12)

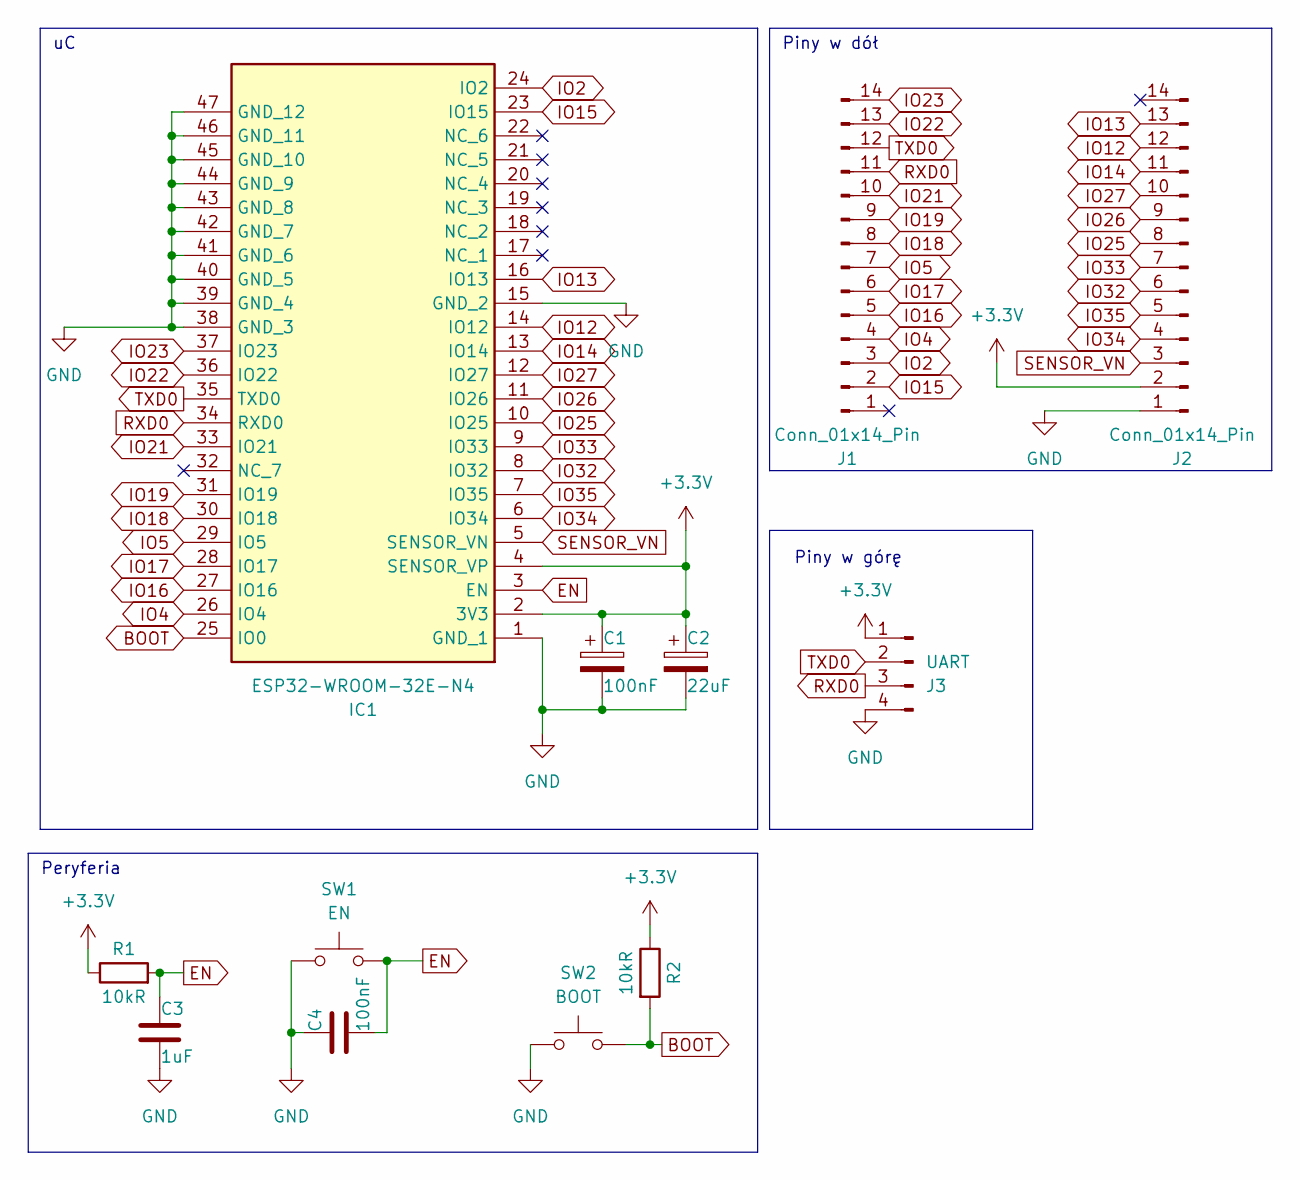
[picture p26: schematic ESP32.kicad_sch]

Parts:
C1, C4: 100nF; C_0402_1005Metric_Pad0.74x0.62mm_HandSolder
C2: 22uF; C_0402_1005Metric_Pad0.74x0.62mm_HandSolder
C3: 1uF; C_0402_1005Metric_Pad0.74x0.62mm_HandSolder
IC1: ESP32-WROOM-32E-N4; ESP32WROOM32EN4; Manufacturer_Part_Number ESP32-WROOM-32E-N4
J1, J2: Conn_01x14_Pin; PinHeader_1x14_P2.54mm_Vertical
J3: UART; PinHeader_1x04_P2.54mm_Vertical
R1, R2: 10kR; R_0402_1005Metric_Pad0.72x0.64mm_HandSolder
SW1: EN; SW_Push_1P1T_XKB_TS-1187A
SW2: BOOT; SW_Push_1P1T_XKB_TS-1187A

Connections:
+3.3V: C1.1, C2.1, IC1.2 (3V3), IC1.4 (SENSOR_VP), J2.2, J3.1, R1.1, R2.1
BOOT: IC1.25 (IO0), R2.2, SW2.2
EN: C3.1, C4.2, IC1.3 (EN), R1.2, SW1.2
GND: C1.2, C2.2, C3.2, C4.1, IC1.1 (GND_1), IC1.15 (GND_2), IC1.38 (GND_3), IC1.39 (GND_4), IC1.40 (GND_5), IC1.41 (GND_6), IC1.42 (GND_7), IC1.43 (GND_8), IC1.44 (GND_9), IC1.45 (GND_10), IC1.46 (GND_11), IC1.47 (GND_12), J2.1, J3.4, SW1.1, SW2.1
IO2: IC1.24 (IO2), J1.3
IO4: IC1.26 (IO4), J1.4
IO5: IC1.29 (IO5), J1.7
IO12: IC1.14 (IO12), J2.12
IO13: IC1.16 (IO13), J2.13
IO14: IC1.13 (IO14), J2.11
IO15: IC1.23 (IO15), J1.2
IO16: IC1.27 (IO16), J1.5
IO17: IC1.28 (IO17), J1.6
IO18: IC1.30 (IO18), J1.8
IO19: IC1.31 (IO19), J1.9
IO21: IC1.33 (IO21), J1.10
IO22: IC1.36 (IO22), J1.13
IO23: IC1.37 (IO23), J1.14
IO25: IC1.10 (IO25), J2.8
IO26: IC1.11 (IO26), J2.9
IO27: IC1.12 (IO27), J2.10
IO32: IC1.8 (IO32), J2.6
IO33: IC1.9 (IO33), J2.7
IO34: IC1.6 (IO34), J2.4
IO35: IC1.7 (IO35), J2.5
RXD0: IC1.34 (RXD0), J1.11, J3.3
SENSOR_VN: IC1.5 (SENSOR_VN), J2.3
TXD0: IC1.35 (TXD0), J1.12, J3.2

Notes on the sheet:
Piny w górę
Piny w dół
Peryferia

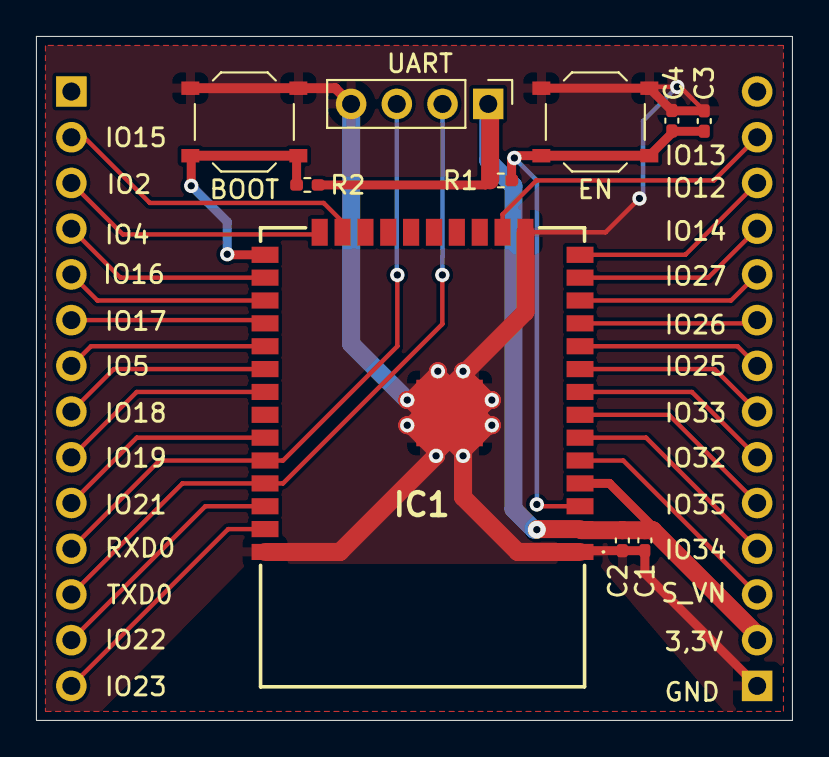
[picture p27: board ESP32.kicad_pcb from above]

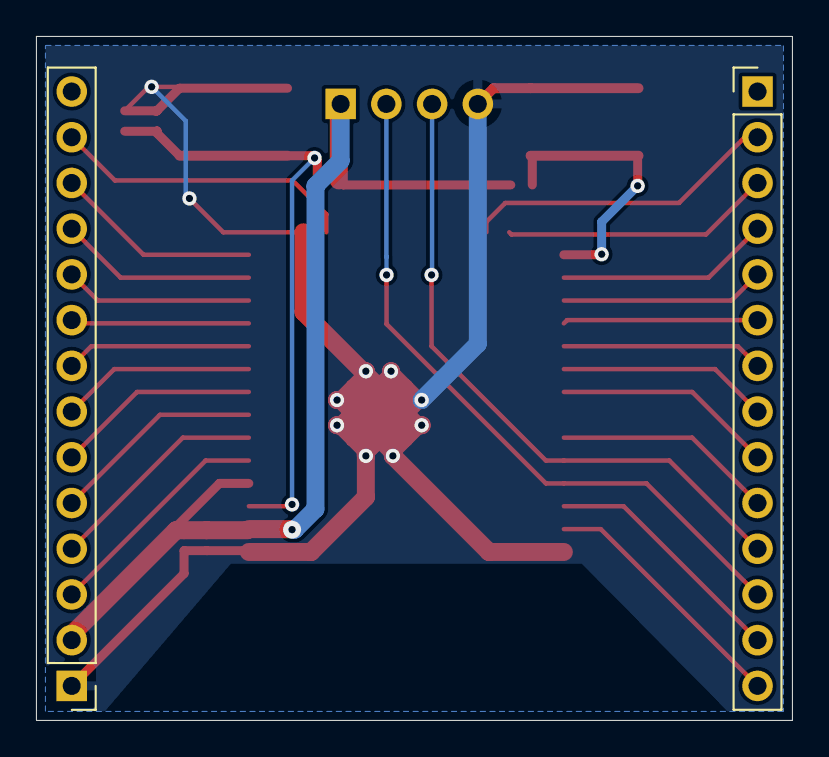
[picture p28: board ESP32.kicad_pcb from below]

Board: 2 copper layers, 42.0 x 38.0 mm, 12 parts (2 on the bottom side), 28 nets.

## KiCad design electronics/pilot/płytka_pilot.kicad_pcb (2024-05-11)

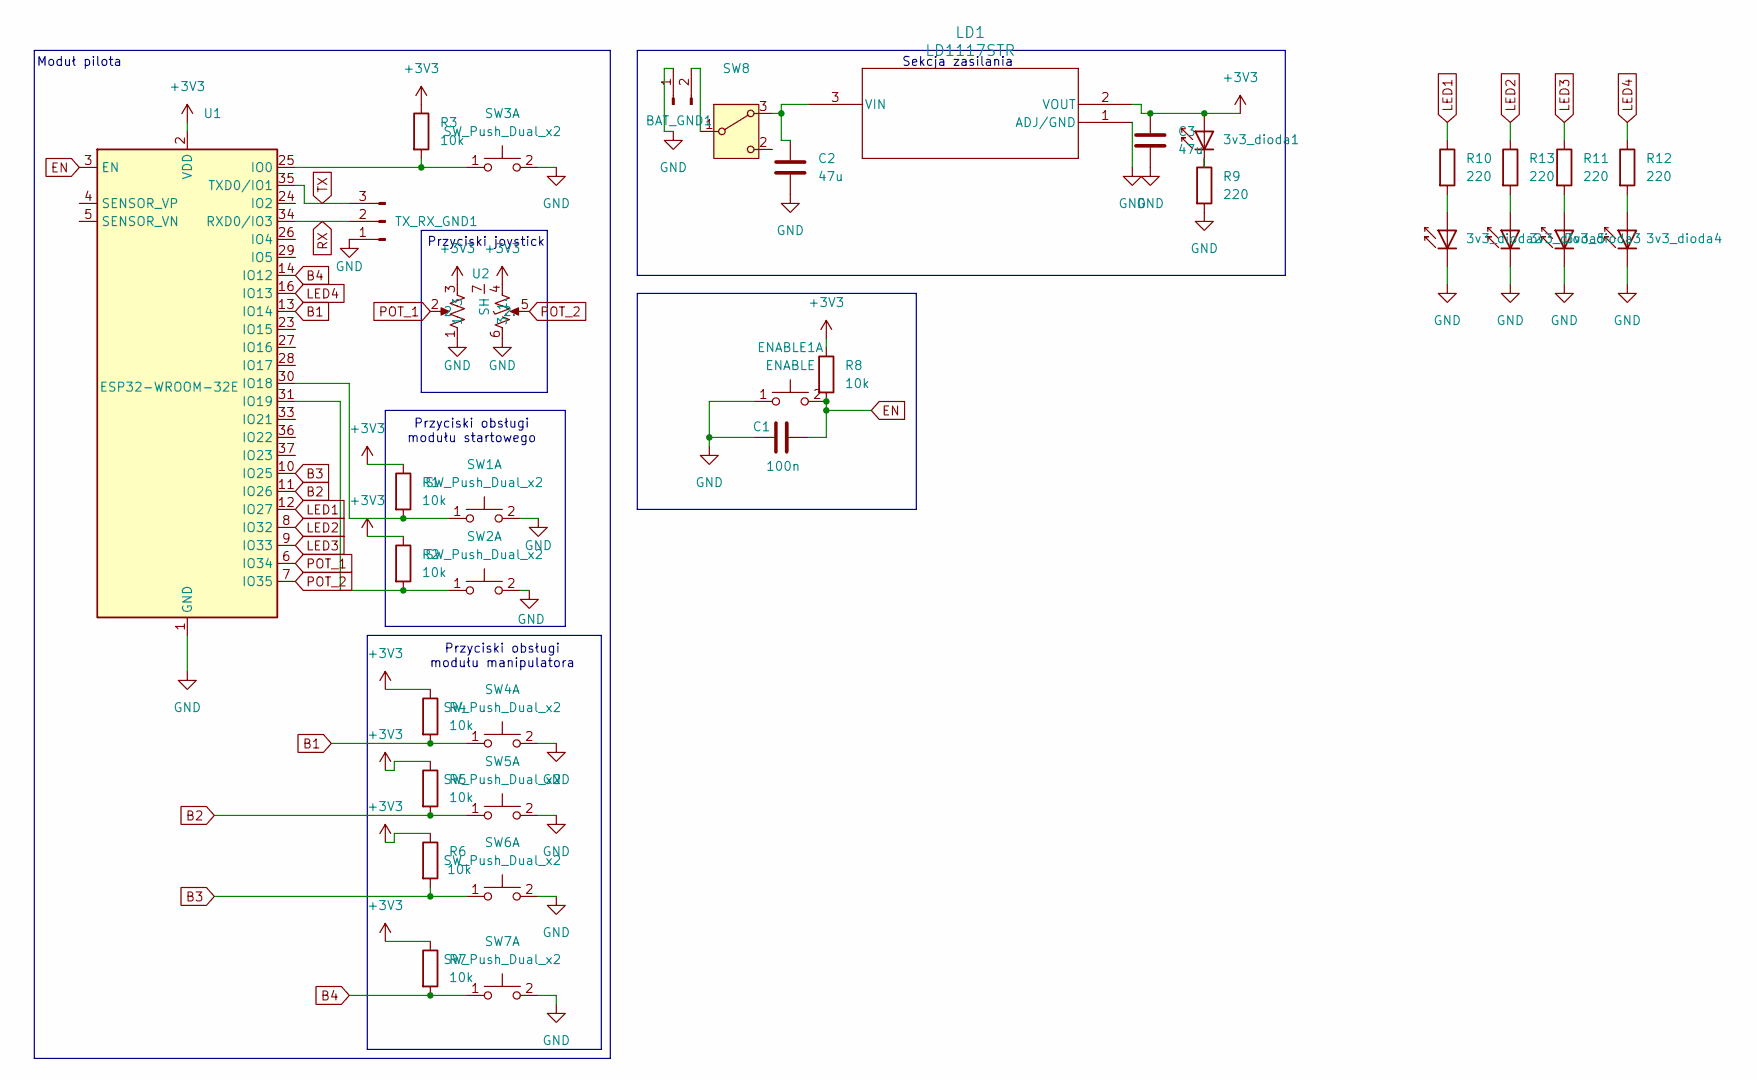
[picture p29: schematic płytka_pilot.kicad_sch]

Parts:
3v3_dioda1, 3v3_dioda2, 3v3_dioda3, 3v3_dioda4, 3v3_dioda5: IR204A; LED_D3.0mm_IRBlack
BAT_GND1: Conn_01x02_Pin; PinHeader_1x02_P2.54mm_Vertical
C1: 100n; C_0603_1608Metric
C2, C3: 47u; CP_EIA-3528-21_Kemet-B_Pad1.50x2.35mm_HandSolder
ENABLE1: ENABLE; SW_Push_1P1T_XKB_TS-1187A
LD1: LD1117STR; SOT-223
R1, R2, R3, R4, R5, R6, R7, R8: 10k; R_0603_1608Metric
R9, R10, R11, R12, R13: 220; R_0603_1608Metric
SW1, SW2, SW4, SW5, SW6, SW7: SW_Push_Dual_x2; SW_PUSH_6mm
SW3: SW_Push_Dual_x2; SW_Push_1P1T_XKB_TS-1187A
SW8: SW_Wuerth_450301014042; SW_Slide-03_Wuerth-WS-SLTV_10x2.5x6.4_P2.54mm
TX_RX_GND1: Conn_01x03_Pin; PinSocket_1x03_P2.54mm_Vertical
U1: ESP32-WROOM-32E; ESP32-WROOM-32D
U2: 3D161

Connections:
+3V3: 3v3_dioda1.2 (A), C3.1, LD1.2 (VOUT), R1.1, R2.1, R3.1, R4.1, R5.1, R6.1, R7.1, R8.1, U1.2 (VDD), U2.3, U2.4 (1.)
B1: R4.2, SW4.1 (C), U1.13 (IO14)
B2: R5.2, SW5.1 (C), U1.11 (IO26)
B3: R6.2, SW6.1 (C), U1.10 (IO25)
B4: R7.2, SW7.1 (C), U1.14 (IO12)
EN: C1.2, ENABLE1.2 (D), R8.2, U1.3 (EN); also elsewhere on the board
GND: 3v3_dioda2.1 (K), 3v3_dioda3.1 (K), 3v3_dioda4.1 (K), 3v3_dioda5.1 (K), BAT_GND1.1, C1.1, C2.2, C3.2, ENABLE1.1 (C), LD1.1 (ADJ/GND), R9.2, SW1.2 (D), SW2.2 (D), SW3.2 (D), SW4.2 (D), SW5.2 (D), SW6.2 (D), SW7.2 (D), TX_RX_GND1.1, U1.1 (GND), U1.15 (GND), U1.38 (GND), U1.39 (GND), U2.1, U2.6 (3.); also elsewhere on the board
LED1: R10.1, U1.12 (IO27)
LED2: R13.1, U1.8 (IO32)
LED3: R11.1, U1.9 (IO33)
LED4: R12.1, U1.16 (IO13)
unnamed: 3v3_dioda1.1 (K), R9.1
unnamed: 3v3_dioda2.2 (A), R10.2
unnamed: 3v3_dioda3.2 (A), R11.2
unnamed: 3v3_dioda4.2 (A), R12.2
unnamed: 3v3_dioda5.2 (A), R13.2
unnamed: BAT_GND1.2, SW8.1 (B)
unnamed: C2.1, LD1.3 (VIN), SW8.3 (A)
unnamed: R1.2, SW1.1 (C), U1.30 (IO18)
unnamed: R2.2, SW2.1 (C), U1.31 (IO19)
unnamed 20: R3.2, SW3.1 (C), U1.25 (IO0); also elsewhere on the board
POT_1: U1.6 (IO34), U2.2
POT_2: U1.7 (IO35), U2.5 (2.)
RX: TX_RX_GND1.2, U1.34 (RXD0/IO3)
TX: TX_RX_GND1.3, U1.35 (TXD0/IO1)

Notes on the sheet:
Moduł pilota
Przyciski joystick
Przyciski obsługi modułu startowego
Sekcja zasilania
Przyciski obsługi modułu manipulatora

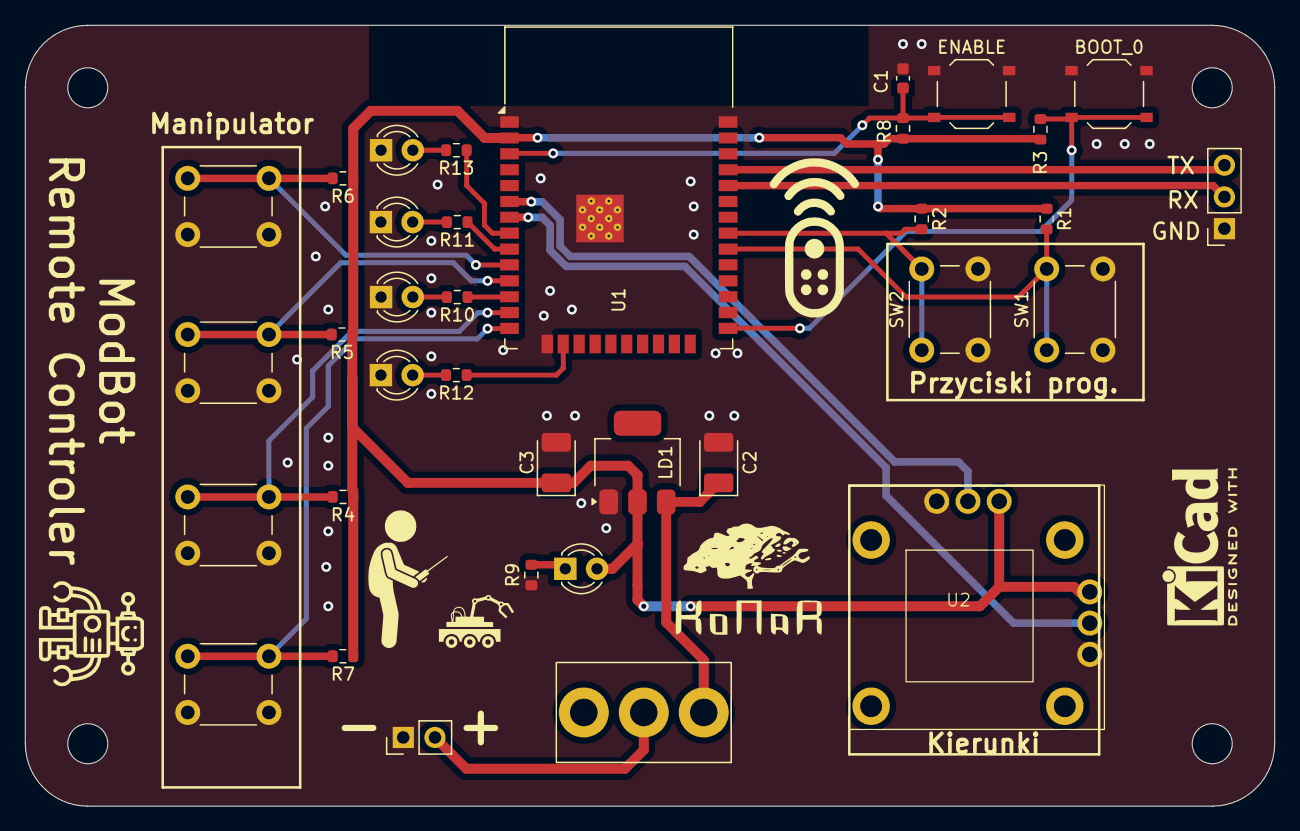
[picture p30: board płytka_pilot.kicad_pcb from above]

Board: 2 copper layers, 100.0 x 62.5 mm, 35 parts (0 on the bottom side), 25 nets.

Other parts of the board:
BOOT_0: SW_Push_Dual_x2; SW_Push_1P1T_XKB_TS-1187A
ENABLE: ENABLE; SW_Push_1P1T_XKB_TS-1187A

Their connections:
EN: ENABLE.2 (D); also elsewhere on the board
GND: BOOT_0.2 (D), ENABLE.1 (C); also elsewhere on the board
unnamed 20: BOOT_0.1 (C); also elsewhere on the board

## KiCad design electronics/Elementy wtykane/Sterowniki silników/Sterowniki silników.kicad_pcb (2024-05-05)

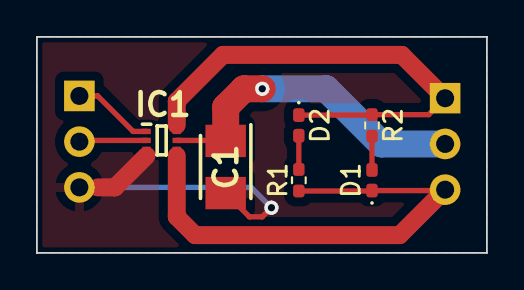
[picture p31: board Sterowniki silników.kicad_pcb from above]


Board: 2 copper layers, 25.0 x 12.0 mm, 8 parts (2 on the bottom side), 8 nets.

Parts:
C1: C_Polarized; CAPPM3528X210N
D1, D2: LED; D_0402_1005Metric_Pad0.77x0.64mm_HandSolder
IC1: DRV8210DRLR; SOTFL50P160X60-6N
J1, J2: Conn_01x03_Pin; PinHeader_1x03_P2.54mm_Vertical
R1, R2: 500R; R_0402_1005Metric_Pad0.72x0.64mm_HandSolder

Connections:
GND: C1.2, IC1.3 (GND), J1.3
unnamed: D1.2 (A), R2.2
unnamed: D2.2 (A), R1.2
PWM_DRV1: IC1.1 (IN1), J1.1
PWM_DRV2: IC1.2 (IN2), J1.2
VDD: C1.1, IC1.5 (VM), J2.2
V_M1: D2.1 (K), IC1.6 (OUT1), J2.1, R2.1
V_M2: D1.1 (K), IC1.4 (OUT2), J2.3, R1.1

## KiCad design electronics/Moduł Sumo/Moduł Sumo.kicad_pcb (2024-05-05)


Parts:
C1: 22uF; C_0402_1005Metric_Pad0.74x0.62mm_HandSolder
C2, C4: 100nF; C_0402_1005Metric_Pad0.74x0.62mm_HandSolder
J1: Input; JST_EH_B4B-EH-A_1x04_P2.50mm_Vertical
J2: OUT 1; PinHeader_1x04_P2.54mm_Vertical
J3: OUT 2; PinHeader_1x04_P2.54mm_Vertical
J4: OUT 3; PinHeader_1x04_P2.54mm_Vertical
J5: OUT 4; PinHeader_1x04_P2.54mm_Vertical
J6: RST_M; PinSocket_1x02_P2.54mm_Vertical
J7: Sense_OUT; JST_EH_B4B-EH-A_1x04_P2.50mm_Vertical
R1, R2, R3, R4, R5, R6, R7, R8, R12, R13, R35: 2,2kR; R_0402_1005Metric_Pad0.72x0.64mm_HandSolder
U1: TCA9548APWR; TSSOP-24_4.4x7.8mm_P0.65mm

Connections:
+3.3V: C1.1, C2.1, J1.1, J2.1, J3.1, J4.1, J5.1, J7.1, R1.1, R2.1, R3.1, R4.1, R5.1, R6.1, R7.1, R8.1, R12.1, R13.1, R35.1, U1.24 (VCC)
GND: C1.2, C2.2, C4.2, J1.4, J2.2, J3.2, J4.2, J5.2, J6.2, J7.4, U1.1 (A0), U1.2 (A1), U1.12 (GND), U1.21 (A2)
RST_M: C4.1, J6.1, R35.2, U1.3 (~RESET)
SC0: J7.3, R1.2, U1.5 (SC0)
SC1: J2.3, R3.2, U1.7 (SC1)
SC2: J3.3, R5.2, U1.9 (SC2)
SC3: J4.3, R7.2, U1.11 (SC3)
SC4: J5.3, R12.2, U1.14 (SC4)
SCL: J1.3, U1.22 (SCL)
SD0: J7.2, R2.2, U1.4 (SD0)
SD1: J2.4, R4.2, U1.6 (SD1)
SD2: J3.4, R6.2, U1.8 (SD2)
SD3: J4.4, R8.2, U1.10 (SD3)
SD4: J5.4, R13.2, U1.13 (SD4)
SDA: J1.2, U1.23 (SDA)

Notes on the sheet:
Złącza Reset
Złącza WE/WY
Multiplekser I2C
Pullup I2C



Board: 2 copper layers, 31.3 x 34.0 mm, 22 parts (13 on the bottom side), 15 nets.

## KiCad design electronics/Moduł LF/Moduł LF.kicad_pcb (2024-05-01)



Board: 2 copper layers, 42.0 x 24.2 mm, 23 parts (12 on the bottom side), 19 nets.

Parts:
D1, D2, D3, D4: LED; LED_0402_1005Metric_Pad0.77x0.64mm_HandSolder
J1: Conn_01x06_Socket; JST_XH_B6B-XH-AM_1x06_P2.50mm_Vertical
R1, R6, R7, R12: 330R; R_0402_1005Metric_Pad0.72x0.64mm_HandSolder
R2, R4, R8, R9: 22kR; R_0402_1005Metric_Pad0.72x0.64mm_HandSolder
R3, R5, R10, R11: 110R; R_0402_1005Metric_Pad0.72x0.64mm_HandSolder
RV1: R_Potentiometer; Potencjometr 3,2x3,4
U1: LM2901; SOIC127P600X175-14N
U2, U3, U4, U5: ITR8307-S17-TR8; Everlight_ITR1201SR10AR

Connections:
+3.3V: J1.1, R1.1, R6.1, R7.1, R12.1, RV1.1, U1.3 (V+), U2.2 (A), U2.3, U3.2 (A), U3.3, U4.2 (A), U4.3, U5.2 (A), U5.3
GND: J1.6, R2.2, R3.2, R4.2, R5.2, R8.2, R9.2, R10.2, R11.2, RV1.3, U1.12 (V-)
unnamed: D1.2 (A), R12.2
unnamed: D1.1 (K), J1.5, U1.14
unnamed: D2.2 (A), R1.2
unnamed: D2.1 (K), J1.4, U1.13
unnamed: D3.2 (A), R6.2
unnamed: D3.1 (K), J1.2, U1.2
unnamed: D4.2 (A), R7.2
unnamed: D4.1 (K), J1.3, U1.1
unnamed: R3.1, U2.1 (K)
unnamed: R5.1, U3.1 (K)
unnamed: R10.1, U4.1 (K)
unnamed: R11.1, U5.1 (K)
SIGNAL_IR_01: R2.1, U1.5 (+), U2.4
SIGNAL_IR_02: R4.1, U1.7 (+), U3.4
SIGNAL_IR_03: R8.1, U1.11 (+), U4.4
SIGNAL_IR_04: R9.1, U1.9 (+), U5.4
V_REF_IR: RV1.2, U1.4 (-), U1.6 (-), U1.8 (-), U1.10 (-)

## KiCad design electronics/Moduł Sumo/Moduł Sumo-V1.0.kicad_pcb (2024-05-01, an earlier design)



Board: 2 copper layers, 62.0 x 29.5 mm, 51 parts (11 on the bottom side), 38 nets.

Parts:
C1: 22uF; C_0402_1005Metric_Pad0.74x0.62mm_HandSolder
C2, C3, C4: 100nF; C_0402_1005Metric_Pad0.74x0.62mm_HandSolder
D1, D2, D3, D4, D5, D6, D7, D8: LED; LED_0402_1005Metric_Pad0.77x0.64mm_HandSolder
IC1: MCP23018-E_SO; SOIC127P1030X265-28N
J1: Input; JST_EH_B4B-EH-A_1x04_P2.50mm_Vertical
J2: OUT 1; PinHeader_1x04_P2.54mm_Vertical
J3: OUT 2; PinHeader_1x04_P2.54mm_Vertical
J4: OUT 3; PinHeader_1x04_P2.54mm_Vertical
J5: OUT 4; PinHeader_1x04_P2.54mm_Vertical
J6: RST_M; PinSocket_1x02_P2.54mm_Vertical
J7: RST_E; PinSocket_1x02_P2.54mm_Vertical
R1, R2, R3, R4, R5, R6, R7, R8, R12, R13, R34, R35: 2,2kR; R_0402_1005Metric_Pad0.72x0.64mm_HandSolder
R20: 1kR; R_0402_1005Metric_Pad0.72x0.64mm_HandSolder
R21: 15kR; R_0402_1005Metric_Pad0.72x0.64mm_HandSolder
R22, R24: 110R; R_0402_1005Metric_Pad0.72x0.64mm_HandSolder
R23, R25: 22kR; R_0402_1005Metric_Pad0.72x0.64mm_HandSolder
R26, R27, R28, R29, R30, R31, R32, R33: 330R; R_0402_1005Metric_Pad0.72x0.64mm_HandSolder
RV1: 10kR; Potencjometr 3,2x3,4
U1: TCA9548APWR; TSSOP-24_4.4x7.8mm_P0.65mm
U2, U3: ITR8307-S17-TR8; Everlight_ITR1201SR10AR
U4: LM2901; SOIC127P600X175-14N

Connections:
+3.3V: C1.1, C2.1, IC1.11 (VDD), J1.1, J2.1, J3.1, J4.1, J5.1, R1.1, R2.1, R3.1, R4.1, R5.1, R6.1, R7.1, R8.1, R12.1, R13.1, R20.1, R26.1, R27.1, R28.1, R29.1, R30.1, R31.1, R34.1, R35.1, RV1.1, U1.24 (VCC), U2.2 (A), U2.3, U3.2 (A), U3.3, U4.3 (V+)
GND: C1.2, C2.2, C3.2, C4.2, D7.1 (K), D8.1 (K), IC1.1 (VSS), IC1.7 (GPB4), IC1.8 (GPB5), IC1.9 (GPB6), IC1.10 (GPB7), IC1.22 (GPA2), IC1.23 (GPA3), IC1.24 (GPA4), IC1.25 (GPA5), IC1.26 (GPA6), IC1.27 (GPA7), J1.4, J2.2, J3.2, J4.2, J5.2, J6.2, J7.2, R21.2, R22.2, R23.2, R24.2, R25.2, RV1.3, U1.1 (A0), U1.2 (A1), U1.12 (GND), U1.21 (A2), U4.12 (V-)
GPA0: D2.1 (K), IC1.20 (GPA0), U4.1
GPA1: D1.1 (K), IC1.21 (GPA1), U4.2
GPB0: D3.1 (K), IC1.3 (GPB0)
GPB1: D4.1 (K), IC1.4 (GPB1)
GPB2: D5.1 (K), IC1.5 (GPB2)
GPB3: D6.1 (K), IC1.6 (GPB3)
INTA: IC1.19 (INTA), R33.1
INTB: IC1.18 (INTB), R32.1
IR_SENSE0: R23.1, U2.4, U4.7 (+)
IR_SENSE1: R25.1, U3.4, U4.5 (+)
unnamed: D1.2 (A), R26.2
unnamed: D2.2 (A), R27.2
unnamed: D3.2 (A), R28.2
unnamed: D4.2 (A), R29.2
unnamed: D5.2 (A), R30.2
unnamed: D6.2 (A), R31.2
unnamed: D7.2 (A), R32.2
unnamed: D8.2 (A), R33.2
unnamed: IC1.15 (ADDR), R20.2, R21.1
unnamed: R22.1, U2.1 (K)
unnamed: R24.1, U3.1 (K)
RST_E: C3.1, IC1.16 (~RESET), J7.1, R34.2
RST_M: C4.1, J6.1, R35.2, U1.3 (~RESET)
SC0: IC1.12 (SCL), R1.2, U1.5 (SC0)
SC1: J2.3, R3.2, U1.7 (SC1)
SC2: J3.3, R5.2, U1.9 (SC2)
SC3: J4.3, R7.2, U1.11 (SC3)
SC4: J5.3, R12.2, U1.14 (SC4)
SCL: J1.3, U1.22 (SCL)
SD0: IC1.13 (SDA), R2.2, U1.4 (SD0)
SD1: J2.4, R4.2, U1.6 (SD1)
SD2: J3.4, R6.2, U1.8 (SD2)
SD3: J4.4, R8.2, U1.10 (SD3)
SD4: J5.4, R13.2, U1.13 (SD4)
SDA: J1.2, U1.23 (SDA)
V_REF: RV1.2, U4.4 (-), U4.6 (-)

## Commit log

2024-04-04 pierwszy model 3D
    [MAIN_MODULE.0003.iam, MAIN_MODULE.iam, N20 DC MOTOR.ipt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]
2024-04-25 Utworzono pliki na schematy elektroniczne
    [ESP32.kicad_pcb, ESP32.kicad_sch, Moduł LF.kicad_pcb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]
2024-04-25 Dodano schematy sterownika silników, oraz modułu LF
    [Moduł LF.kicad_sch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]
2024-04-25 Dodano notatki dotyczące zmian
    [Sterowniki silników.kicad_sch]
2024-04-26 Dalsze zmiany w elektronice
    [293D476X9010B2TE3.stp, EDI2CAP.CFG, ESP32.kicad_sch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]
2024-04-26 Dodano schemat i footprint do ESP32
    [DTSM-31N-V-T_R.stp, ESP32.kicad_pcb, ESP32.kicad_sch]
2024-04-26 Rozpoczęto pracę nad płytką minisumo
    [Moduł Sumo.kicad_pcb, Moduł Sumo.kicad_sch]
2024-04-27 wstepna mechanika
    [Li_Pol 800mAh.0002.ipt, Li_Pol 800mAh.ipt, MAIN.0003.iam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]
2024-04-27 Ukończenie modułu LF
    [Moduł LF.kicad_pcb, Moduł LF.kicad_sch]
2024-04-27 Poprawiono moduł Sumo i Dokończono moduł Hub LF
    [Hub LF.kicad_pcb, Hub LF.kicad_sch, MCP23018-E_SO.stp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]
2024-04-28 first mechanical project of main module
    [MAIN.0003.iam, MAIN.0005.iam, MAIN.iam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]
2024-04-28 drobne zmiany w mechanice
    [MAIN.0005.iam, MAIN.0006.iam, MAIN.iam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]
2024-04-28 dodano stl
    [dach.stl, druk.3mf, literka.stl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]
2024-04-29 Utworzono modul sumo
    [1x4 Male Pin Header Angle.STEP, 1x4 Male Pin Header Angle.ipt, 1x4 Male Pin Header Angle_MIR.ipt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]
2024-04-30 Ukończono moduł sumo
    [Moduł Sumo.kicad_pcb, Moduł Sumo.kicad_sch, Płytka główna.kicad_sch]
2024-04-30 Poprawiono płytkę ESP32
    [ESP32.kicad_pcb, ESP32.kicad_sch, Sterowniki silników.kicad_pcb]
2024-05-01 Poprawiono płytki LF, zmieniono podejście do MiniSumo
    [Hub LF.kicad_pcb, Moduł LF.kicad_pcb, Moduł Sumo-V1.0.kicad_pcb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]
2024-05-01 Zmiana koncepcji płytki od minisumo
    [Moduł Sumo.kicad_pcb, Moduł Sumo.kicad_sch]
2024-05-01 Dokończono alternatywną wersję płytki minisumo
    [Moduł Sumo.kicad_pcb, Moduł Sumo.kicad_sch]
2024-05-03 Wstępne zrobienie komunikacji, oraz zasilania
    [ESP32.kicad_pcb, MCP73844-840I_MS.stp, MIC2288YD5-TR.stp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]
2024-05-04 Funkcjonalna płytka główna
    [Płytka główna.kicad_sch, elemanty_wtykane.kicad_sch, komunikacja.kicad_sch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]
2024-05-04 Ukończono płytkę główną
    [Płytka główna.kicad_pcb, elemanty_wtykane.kicad_sch]
2024-05-05 Zmieniono wartości rezystorów i wygenerowano wstepną listę elementów do kupienia
    [ESP32.csv, ESP32.kicad_sch, Hub LF.csv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]
2024-05-05 I have added footprint for joystick
2024-05-05 Dokonano panelizacji i wykonano pliki wierceń
    [ESP32.kicad_pcb, Hub LF.kicad_pcb, Moduł Sumo.kicad_pcb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]
2024-05-11 dodano plytke pilota
    [płytka_pilot.kicad_pcb, płytka_pilot.kicad_sch]
2024-05-12 rozpoczeto prace nad chwytakiem
    [A1.SLDPRT, A1.ipt, Base.ipt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]
2024-05-25 Dodano model 3D modulu LF i chwytaka
    [ESP32.0001.ipt, ESP32.ipt, Hub LF.ipt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]
2024-05-26 poprawki w chwytaku i przygotowanie do druku
    [Base.stl, Claw.stl, Connector.stl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]
2024-06-22 poprawki w mechanice
    [2.iam, Hub LF.0001.ipt, Hub LF.ipt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]
